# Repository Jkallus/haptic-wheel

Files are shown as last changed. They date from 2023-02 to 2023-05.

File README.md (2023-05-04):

# Haptic Volume Knob
Haptic feedback wheel implementing a volume knob. Inspired by Scott Bezek's Smart Knob and University of Michigan EECS 461 Haptics Lab

This volume knob is implemented with a feedback controlled motor and software rather than mechanical notches. When you turn it with your hand you feel real feedback force just as if it were an actual precisely made mechanical knob. Haptic Volume Knob works by monitoring the motor shaft's angle and applying the appropriate torque to implement the knob's feeling for that position. An ESP32 S3 monitors this position and commands a torque 7,000 times per second to give real time feedback that is convincing to a user as well as implements a stable control loop.

Two haptic effects are implemented here: A virtual knob with detents and a virtual wall which creates the sensation of the knob reaching end of travel. These sensations can be customized to feel "harder" or "softer" depending on spring constants. There is a button on the back of the enclosure to iterate through different knob detent feelings ranging from very light to very stiff. This variable haptic effect cannot be acheived with a traditional knob. 

The ESP32 communicates with the PC using HID. The TinyUSB HID library allows the ESP32 to describe itself as a custom HID device. It sends volume updates to Windows in the same way as the volume up and down keys on any keyboard work. The ESP32 gets the initial volume and any updates to the volume level made elsewhere by a service running on Windows which monitors volume changes and sends updates as HID reports. 

# Bill of Materials
| Item | Source | | | |
|---|---|---|---|---|
| ESP32 S3 | https://www.amazon.com/Teyleten-Robot-ESP32-S3-DevKitC-1-N8R2-Development-Integrates/dp/B0B6HT7V7P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 | | | |
| Busboard ST2 | https://www.amazon.com/Busboard-ST2-Traditional-Stripboard-Prototyping/dp/B00LLQFRAU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 | | | |
| TMC6300 Brushless Motor Driver  | https://www.sparkfun.com/products/retired/21220 | | | |
| Three Phase Brushless Motor | https://www.sparkfun.com/products/20441 | | | |
| AS5048A Magnetic Rotary Encoder | https://www.digikey.com/en/products/detail/ams-osram/AS5048A-TS-EK-AB/3188612 | | | |
| Neopixel 24 LED Ring | https://www.adafruit.com/product/1586 | | | |
| BH1750 Light Sensor | https://www.amazon.com/ACEIRMC-BH1750FVI-Intensity-Illumination-arduino/dp/B08ZS4PJSW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 | | | |
| LM2596 Buck Converter | https://www.amazon.com/Converter-Adjustable-Regulator-Efficiency-Transformer/dp/B08L5VRBZS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 | | | |
| Panel Mount Button | https://www.amazon.com/dp/B0752RMB7Q?psc=1&ref=ppx_yo2ov_dt_b_product_details | | | |
| DC Socket | https://www.amazon.com/dp/B082GHXS1Q?psc=1&ref=ppx_yo2ov_dt_b_product_details | | | |
| Micro USB Female Breakout | https://www.amazon.com/gp/product/B07T91S7L2/ref=ppx_yo_dt_b_search_asin_title?ie=UTF8&psc=1 | | | |
| PH 2.0 Crimp | https://www.amazon.com/gp/product/B07VHCFGZS/ref=ppx_yo_dt_b_search_asin_title?ie=UTF8&psc=1 | | | |
| | | | | |
| | | | | |

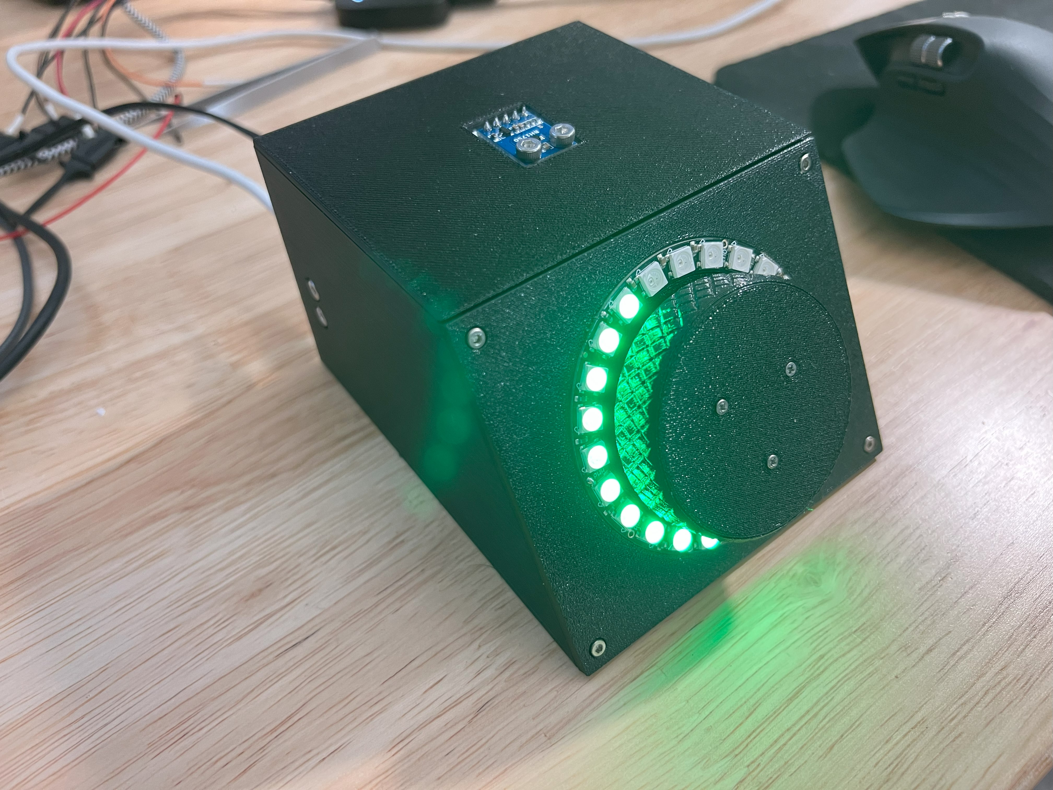
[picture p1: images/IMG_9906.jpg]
View 1

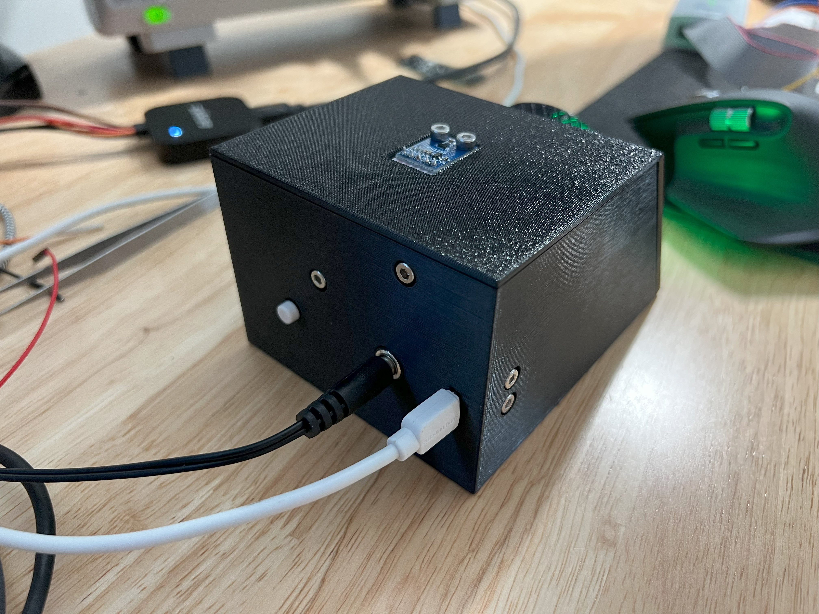
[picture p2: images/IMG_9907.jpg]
View 2

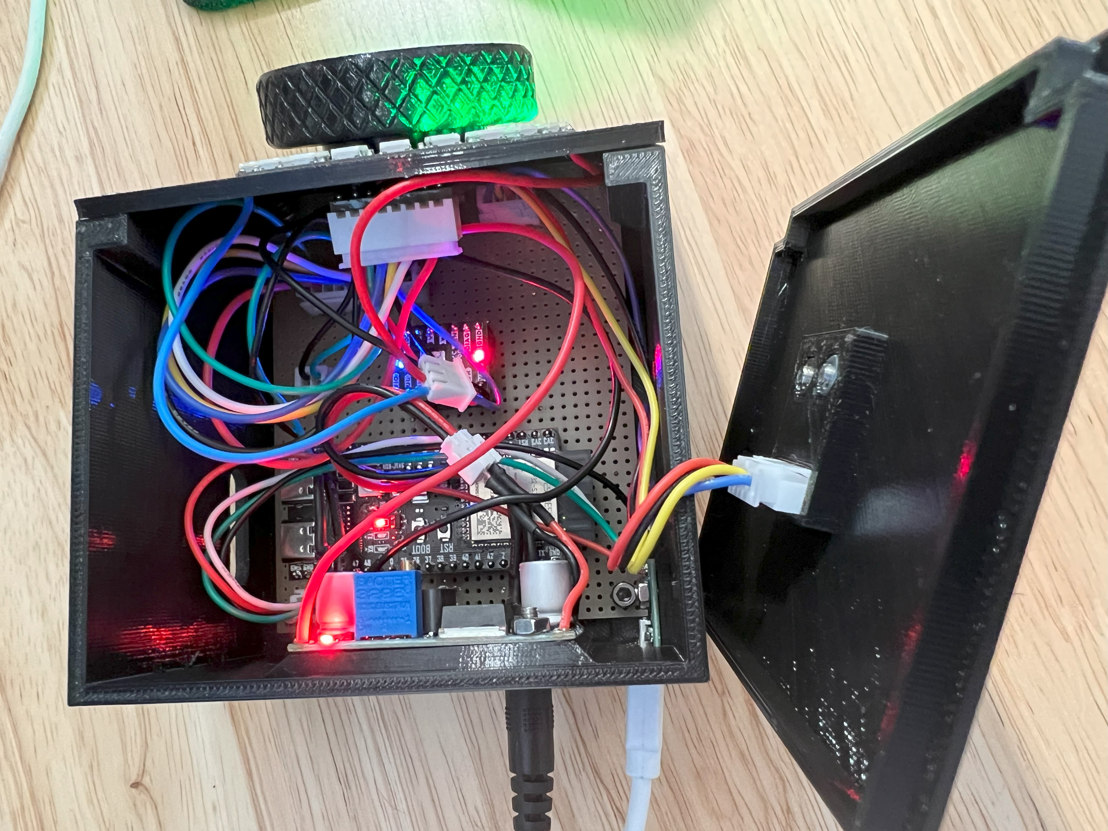
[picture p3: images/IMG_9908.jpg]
View 3


# Install Service
In powershell run the following line replacing paths with your own
`New-Service -Name "HIDVolumeSync" -BinaryPathName "C:\Users\joshk\source\repos\haptic-wheel\HID Volume Sync Service\bin\Debug\HID Volume Sync Service.exe"`
 
Make sure the service is set to startup type automatic in the Windows Services UI to start on boot up.

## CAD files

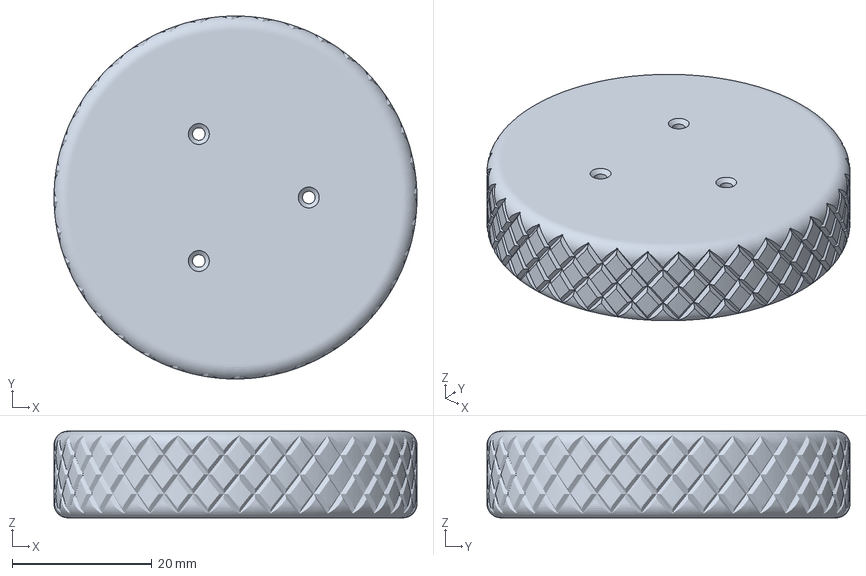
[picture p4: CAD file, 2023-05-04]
cad/Final Knob.3MF
52.0 x 52.0 x 12.4 mm

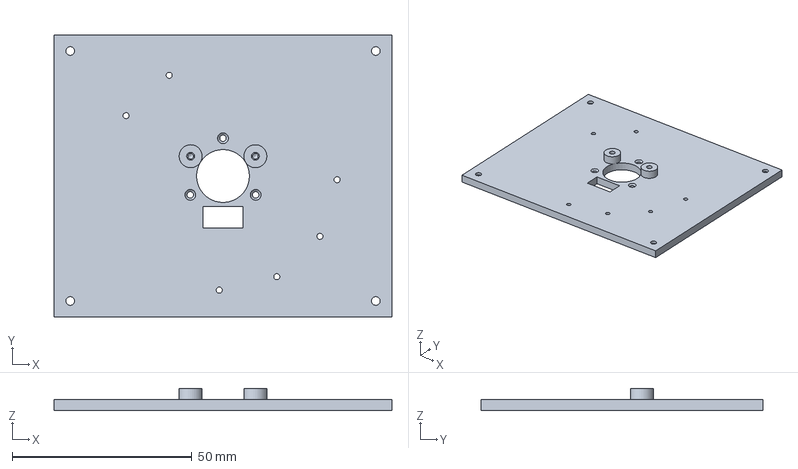
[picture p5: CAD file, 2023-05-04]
cad/Wheel Face.3MF
94.0 x 78.5 x 6.12 mm

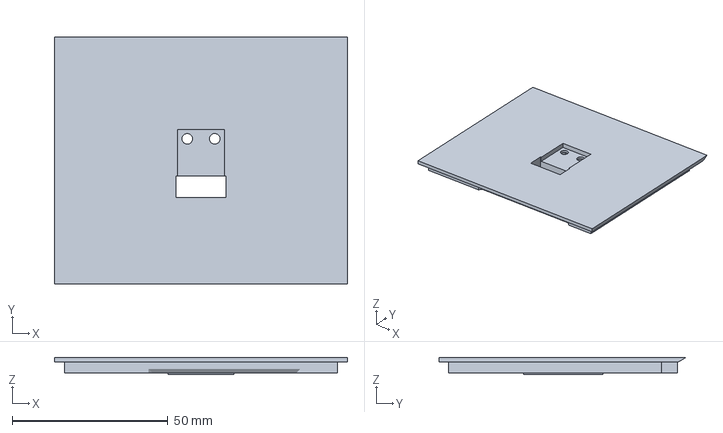
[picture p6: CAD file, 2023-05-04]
cad/Lid.3MF
94.0 x 79.3 x 5.50 mm

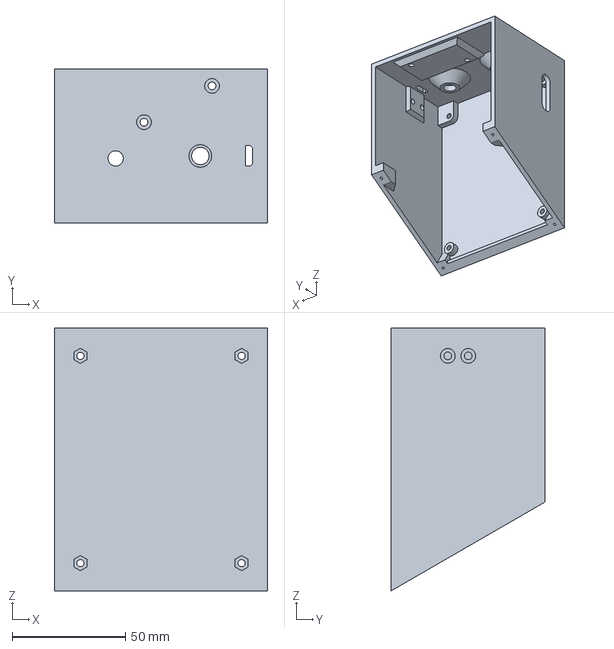
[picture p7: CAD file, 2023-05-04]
cad/Enclosure.3MF
94.0 x 68.0 x 116.0 mm

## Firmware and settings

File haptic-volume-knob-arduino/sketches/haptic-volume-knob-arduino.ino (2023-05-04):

/*
 *  Haptic Volume Knob
 *	MIT License
 *	
 *	Copyright 2023 Josh Kallus
 *	
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
 *	TODO: Check initial setting and make sure its not detecting a change there
 *	TODO: Motor rapidly moves sometimes when volume set externally reaches 100% or 0%
 *	TODO: End of travel angle can move further in a direction when repeatedly going to EOT and backing off. Not a huge deal but should be figured out
 */

#include "USB.h"
#include "USBHID.h"
#include <SimpleFOC.h>
#include <Adafruit_NeoPixel.h>
#include <Wire.h>
#include <BH1750.h>

#ifdef LOG_LOCAL_LEVEL
	#undef LOG_LOCAL_LEVEL
#endif

#define LOG_LOCAL_LEVEL ESP_LOG_WARN

////////////////// HID Config ////////////////////
const char* HID_TAG = "HID";
const char* MOTOR_TAG = "MOTOR";
const char* VOLUME_TAG = "VOLUME";
const char* MAIN_TAG = "MAIN";
const char* LED_TAG = "LED";
const char* BUTTON_TAG = "BUTTON";
static const uint8_t report_descriptor[] = { // 8 axis
    0x05, 0x0C,    // UsagePage(Consumer[12])
    0x09, 0x01,    // UsageId(Consumer Control[1])
    0xA1, 0x01,    // Collection(Application)
    0x85, 0x01,    //     ReportId(1)
    0x09, 0xE9,    //     UsageId(Volume Increment[233])
    0x15, 0x00,    //     LogicalMinimum(0)
    0x25, 0x01,    //     LogicalMaximum(1)
    0x95, 0x01,    //     ReportCount(1)
    0x75, 0x01,    //     ReportSize(1)
    0x81, 0x02,    //     Input(Data, Variable, Absolute, NoWrap, Linear, PreferredState, NoNullPosition, BitField)
    0x09, 0xEA,    //     UsageId(Volume Decrement[234])
    0x81, 0x02,    //     Input(Data, Variable, Absolute, NoWrap, Linear, PreferredState, NoNullPosition, BitField)
    0x75, 0x06,    //     ReportSize(6)
    0x81, 0x03,    //     Input(Constant, Variable, Absolute, NoWrap, Linear, PreferredState, NoNullPosition, BitField)
    0x09, 0xE0,    //     UsageId(Volume[224])
    0x15, 0xFF,    //     LogicalMinimum(-1)
    0x75, 0x02,    //     ReportSize(2)
    0x91, 0x02,    //     Output(Data, Variable, Absolute, NoWrap, Linear, PreferredState, NoNullPosition, NonVolatile, BitField)
    0x75, 0x06,    //     ReportSize(6)
    0x91, 0x03,    //     Output(Constant, Variable, Absolute, NoWrap, Linear, PreferredState, NoNullPosition, NonVolatile, BitField)
    0xC0,          // EndCollection()
};
USBHID HID;

////////////////// Motor Config //////////////////
#define A_h 18
#define A_l 8
#define B_h 16
#define B_l 17
#define C_h 7
#define C_l 15

enum class DETENTS_PER_REV
{
	Fifty      = 50,
	TwentyFive = 25,
};

constexpr DETENTS_PER_REV detents_per_revolution = DETENTS_PER_REV::Fifty;
constexpr float detent_width = 360.0f / (float)detents_per_revolution;
float detent_max_ma = 500;
float detent_max_ma_values[] = { 200, 300, 400, 500, 600, 700 };
constexpr float virtual_wall_ma_per_degree = 350;
float ma_per_degree = detent_max_ma / detent_width;

BLDCMotor motor = BLDCMotor(7);
BLDCDriver6PWM driver = BLDCDriver6PWM(A_h, A_l, B_h, B_l, C_h, C_l);
MagneticSensorSPI sensor = MagneticSensorSPI(AS5048_SPI, 10);

float init_angle = 0.0;
float max_angle = 0.0;
float last_current = 0.0;
float last_angle = 0.0;
float max_angle_threshold = 0.0; // angle threshold for CW after count = 50 (likely negative number)
float min_angle_threshold = 0.0; // angle threshold for CCW after count = 0 (likely positive number)
int count = 0; // number of detents were at out of max, 0...50 or 0...25. 
int i = 0; // loop variable
Commander command = Commander(Serial); // instantiate the commander
QueueHandle_t count_queue_handle = NULL;
TaskHandle_t count_change_internal_handle = NULL;

/////////////////////// Button Config //////////////////////////
gpio_num_t button_pin = GPIO_NUM_14;
QueueHandle_t button_message_queue = NULL;
TaskHandle_t button_task_handle = NULL;
unsigned long button_time = 0;
unsigned long last_button_time = 0;
uint32_t button_presses = 0;
void IRAM_ATTR button_isr()
{
	button_time = millis();
	BaseType_t xHigherPriorityTaskWoken = pdFALSE;
	
	if (button_time - last_button_time > 350)
	{
		button_presses++;
		last_button_time = button_time;
		xQueueSendFromISR(button_message_queue, &button_presses, &xHigherPriorityTaskWoken);
		
		if (xHigherPriorityTaskWoken)
		{
			portYIELD_FROM_ISR();
		}
	}
}

//////////////// LED Config ////////////////////////
#define LED_PIN 9
#define LED_COUNT 24
Adafruit_NeoPixel strip(LED_COUNT, LED_PIN, NEO_GRB + NEO_KHZ800);
QueueHandle_t led_state_queue_handle = NULL;
TaskHandle_t led_task_handle = NULL;
int led_order[24] = {7, 8, 9, 10, 11, 12, 13, 14, 15, 16, 17, 18, 19, 20, 21, 22, 23, 0, 1, 2, 3, 4, 5, 6};

//////////////// Light Sensor Config ///////////////////

#define SDA_PIN 38
#define SCL_PIN 37
TaskHandle_t light_monitor_task_handle;
BH1750 lightMeter;

void setup_light_sensor()
{
	ESP_LOGI(LED_TAG, "Setting up light sensor");
	Wire.setPins(SDA_PIN, SCL_PIN);
	Wire.begin();
	if (!lightMeter.begin())
	{
		ESP_LOGE(LED_TAG, "Light sensor failed to start");
	}
}

float get_light_level()
{
	return lightMeter.readLightLevel();
}

int calculate_brightness_for_lux(float lux)
{
	if (lux < 5) // Just computer monitor brightness
	{
		return 10;
	}
	else if (lux < 30) // Just one lamp far away
	{
		return 15;
	}
	else if (lux < 500) // Just one lamp close by
	{
		return 30;
	}
	else if(lux < 3000)
	{
		return 50;
	}
	else if(lux < 10000)
	{
		return 80;
	}
	else
	{
		return 255;
	}
}

int get_best_led_level()
{
	float val = get_light_level();
	int setting = calculate_brightness_for_lux(val);
	ESP_LOGI(LED_TAG, "Measured %f lux, setting LED brightness to %d", val, setting);
	return setting;
}

void light_monitor_task(void* arg)
{
	while (1)
	{
		strip.setBrightness(get_best_led_level());
		vTaskDelay(pdMS_TO_TICKS(1000)); // update brightness every 5 seconds
	}
}

uint8_t ConvertVolumeLevelToCount(uint8_t volume_level) // returns the count associated with a volume level
{
	if (detents_per_revolution == DETENTS_PER_REV::Fifty)
	{
		return volume_level / 2;
	}
	else
	{
		return volume_level / 4;
	}
}
	
uint8_t  ConvertCountToVolumeLevel(uint8_t count)
{
	if (detents_per_revolution == DETENTS_PER_REV::Fifty)
	{
		return count * 2;
	}
	else
	{
		return count * 4;
	}
}

class CustomHIDDevice : public USBHIDDevice {
public:
	CustomHIDDevice(void) {
		static bool initialized = false;
		if (!initialized) {
			initialized = true;
			HID.addDevice(this, sizeof(report_descriptor));
		}
	}
  
	void begin(void) {
		HID.begin();
	}

	void _onOutput(uint8_t report_id, const uint8_t* buffer, uint16_t len) override
	{
		if (!_received_first_volume) // This is the initial volume setting
		{
			_volume_level = buffer[0];
			ESP_LOGI(HID_TAG, "Received first volume data: %d", _volume_level);
			_received_first_volume = true;
			return;
		}
		else // Volume has changed outside of this device or we're getting confirmation of a recent change origination here
		{
			uint8_t new_volume_level = buffer[0];
			//ESP_LOGI(HID_TAG, "Got feedback, _device_volume is %d and new volume received is %d", _volume_level, new_volume_level);
			
			if (new_volume_level == _volume_level) // This is just a message confirming our recent change
			{
				//ESP_LOGI(HID_TAG, "Received data is confirming recent change made by this device");
			}
			else // Volume has adjusted from outside
			{
				//ESP_LOGI(HID_TAG, "Received data is different value and change needs to be accounted for");
				SetVolumeLevelExternal(new_volume_level);
			}
		}
	}
	
	uint8_t GetVolumeLevel()
	{
		return _volume_level;
	}
	
	// Set the volume level from a change that occured outside the system
	void SetVolumeLevelExternal(uint8_t volume)
	{
		send_led_message_volume_level(volume); // Need to set LEDs
		uint8_t new_count = ConvertVolumeLevelToCount(volume);
		count = new_count; // Need to change count to reflect new status
		if (volume == 100) // If external changes have moved it to 100 or 0 percent then the angle limit needs to be set again
		{
			max_angle_threshold = sensor.getSensorAngle() * (180 / PI) - detent_width / 2;
			ESP_LOGI(MOTOR_TAG, "Volume changed from outside and is now at 100, setting CW threshold angle to %f", max_angle_threshold);
		}
		else if (volume == 0)
		{
			min_angle_threshold = sensor.getSensorAngle() * (180 / PI) + detent_width / 2;
			ESP_LOGI(MOTOR_TAG, "Volume changed from outside and is now at 0, setting CCW threshold angle to %f", min_angle_threshold);
		}
		_volume_level = volume;
	}
	
	// Set the volume level from a change that occured inside the system
	void SetVolumeLevelInternal(uint8_t volume) // Assumed to be 0...100 in increments of 2
	{
		// Need to send update over HID
		if (volume > _volume_level) // volume increment
		{
			uint8_t increment_counts = (volume - _volume_level) % 2;
			increment(increment_counts);
		}
		else // volume decrement
		{
			uint8_t decrement_counts = (_volume_level - volume) % 2;
			decrement(decrement_counts);
		}
		send_led_message_volume_level(volume); // Need to set LEDs
		_volume_level = volume;
	}
	
	void block_till_first_volume()
	{
		while (!_received_first_volume)
		{
			vTaskDelay(pdMS_TO_TICKS(10));
		}
	}

	uint16_t _onGetDescriptor(uint8_t* buffer) {
		memcpy(buffer, report_descriptor, sizeof(report_descriptor));
		return sizeof(report_descriptor);
	}

	bool increment(int counts = 1)
	{
		for (int k = 0; k < counts; k++)
		{
			uint8_t data[1];
			data[0] = 0x01;
			HID.SendReport(1, data, 1);
			data[0] = 0x00;
			return HID.SendReport(1, data, 1);	
			ESP_LOGI(VOLUME_TAG, "Incrementing volume");
		}
	}
	
	bool decrement(int counts = 1)
	{
		for (int k = 0; k < counts; k++)
		{
			uint8_t data[1];
			data[0] = 0x02;
			HID.SendReport(1, data, 1);
			data[0] = 0x00;
			return HID.SendReport(1, data, 1);
			ESP_LOGI(VOLUME_TAG, "Decrementing volume");
		}
	}

	bool send(uint8_t * value) {
		return HID.SendReport(0, value, 8);
	}
	
private:
	uint8_t _volume_level = 0;
	bool _received_first_volume = false;
};
CustomHIDDevice Device;

void count_change_internal_task(void* arg) // Receives new count value from queue
{
	int new_count;
	while (1)
	{
		if (xQueueReceive(count_queue_handle, &new_count, (TickType_t)5))
		{
			Device.SetVolumeLevelInternal(ConvertCountToVolumeLevel((uint8_t)new_count)); // how to handle negative count values? Should never occur in practice
		}
	}
}

void button_handler_task(void* arg)
{
	uint32_t value;
	while (1)
	{
		if (xQueueReceive(button_message_queue, &value, (TickType_t)5))
		{
			int idx = value % (sizeof(detent_max_ma_values) / sizeof(detent_max_ma_values[0]));
			detent_max_ma = detent_max_ma_values[idx];
			ma_per_degree = detent_max_ma / detent_width;
			ESP_LOGI(BUTTON_TAG, "Got button press %d, setting current to idx %d, value %f", value, index, detent_max_ma);
		}
		vTaskDelay(pdMS_TO_TICKS(250));
	}
}

void setup_motor()
{
	sensor.init(); // initialise magnetic sensor hardware
	motor.linkSensor(&sensor); // link the motor to the sensor

	// driver config
	driver.voltage_power_supply = 10; // power supply voltage [V]
	driver.init();
	
	// motor config
	motor.linkDriver(&driver); // link driver
	motor.phase_resistance = 5; // this sets align voltage too
	motor.current_limit = 1.0;
	motor.torque_controller = TorqueControlType::voltage;
	motor.controller = MotionControlType::torque; // set motion control loop to be used
	
	Serial.begin(115200); // use monitoring with serial 
	
	motor.init();
	motor.initFOC(); // align sensor and start FOC

	ESP_LOGI(MOTOR_TAG, "Motor ready");
	vTaskDelay(pdMS_TO_TICKS(1000));
	init_angle = sensor.getSensorAngle() * (180 / PI);
	ESP_LOGI(MOTOR_TAG, "Init angle: %d, Max angle: %d", init_angle, max_angle);
}

//////////////////// LED Functions ///////////////////////////////////
void send_led_message_count(uint8_t count)
{
	xQueueSend(led_state_queue_handle, &count, (TickType_t)5);
}

void send_led_message_volume_level(uint8_t volume_level)
{
	send_led_message_count(ConvertVolumeLevelToCount(volume_level));
}
void led_control_task(void* arg) // Receives volume level in detent counts
{
	uint8_t count_received;
	while (1)
	{
		if(xQueueReceive(led_state_queue_handle, &count_received, (TickType_t)5))
		{
			float levels_per_led = (float)detents_per_revolution / (float)LED_COUNT;
			int fully_lit_count = (int)(count_received / levels_per_led);
			float remainder = fmod(count_received, levels_per_led);
			float last_led_percentage = remainder / levels_per_led;
			set_strip(fully_lit_count, last_led_percentage);
		}
		vTaskDelay(10);
	}
}

void set_strip(int fully_lit, float last_percent)
{
	strip.clear();
	for (int j = 0; j < fully_lit; j++)
	{
		strip.setPixelColor(led_order[j], 0, 255, 0);
	}
	if (last_percent > 0.001 && fully_lit < LED_COUNT) 
	{
		int brightness = (int)(last_percent * 255);
		int last_led_idx = led_order[fully_lit]; 
		strip.setPixelColor(last_led_idx, 0, brightness, 0);
	}
	strip.show();
}

void set_strip_single_color(uint8_t red, uint8_t green, uint8_t blue)
{
	for (int i = 0; i < LED_COUNT; i++)
	{
		strip.setPixelColor(i, red, green, blue);
	}
	strip.show();
}

void setup()
{
	Serial.begin(115200);
	ESP_LOGI(MAIN_TAG, "Started setup");
	
	// Setup light sensor to set led strip
	setup_light_sensor();
	
	// Set strip up first to show init sequence
	strip.begin();
	strip.show();
	strip.clear();
	strip.setBrightness(get_best_led_level());
	set_strip_single_color(50, 0, 0);
	
	// Setup USB to begin waiting for first volume
	Device.begin();
	USB.begin();
	
	// This takes a while
	setup_motor();
	pinMode(4, OUTPUT);
	
	// Wait to get volume
	Device.block_till_first_volume();
	uint8_t initial_volume = Device.GetVolumeLevel();
	
	// Count starts at 0 and has range of 0...detents/revolution
	float volume_as_percent = (float)initial_volume / 100.0f;
	int initial_count = (int) (volume_as_percent * (float) detents_per_revolution);
	ESP_LOGI("MOTOR", "Setting inital count to %d", initial_count);
	count = initial_count;
	
	count_queue_handle = xQueueCreate(5, sizeof(int));
	led_state_queue_handle = xQueueCreate(5, sizeof(uint8_t));
	
	pinMode(button_pin, INPUT_PULLUP);
	button_message_queue = xQueueCreate(5, sizeof(uint32_t));
	attachInterrupt(button_pin, button_isr, FALLING);
	
	xTaskCreate(count_change_internal_task, "Count Change Internal Task", 2048, NULL, configMAX_PRIORITIES - 5, &count_change_internal_handle);
	xTaskCreate(led_control_task, "LED control task", 2048, NULL, configMAX_PRIORITIES - 6, &led_task_handle);
	xTaskCreate(light_monitor_task, "Light monitor task", 4096, NULL, configMAX_PRIORITIES - 10, &light_monitor_task_handle);
	xTaskCreate(button_handler_task, "Button monitor task", 2048, NULL, configMAX_PRIORITIES - 9, &button_task_handle);
	
	xQueueSend(count_queue_handle, &count, (TickType_t)5);
}

void loop()
{
	digitalWrite(4, HIGH);
	motor.loopFOC();
	
	float angle_rad = sensor.getAngle();
	float angle = angle_rad * (180 / PI);
	float spring_current = 0;
	float total_current = 0;
	
	float threshold = detent_width / 2;
	float angle_noise_threshold = 0.3;
	
	if (count >= ConvertVolumeLevelToCount(100) && angle < max_angle_threshold)
	{
		float degrees_past_edge = abs(angle - max_angle_threshold);
		spring_current = (virtual_wall_ma_per_degree / 1000.0) * degrees_past_edge * -1;
		motor.move(spring_current);
		return;
	}
	else if (count <= 0 && angle > min_angle_threshold)
	{
		float degrees_past_edge = abs(angle - min_angle_threshold);
		spring_current = (virtual_wall_ma_per_degree / 1000.0) * degrees_past_edge;
		motor.move(spring_current);
		return;
	}
	
	if (angle > 0)
	{
		float phase = fmod(angle, detent_width);
		if (phase < threshold)
		{		
			if (last_current < 0)
			{
				if (abs(phase - threshold) > angle_noise_threshold)
				{
					spring_current = phase * (ma_per_degree / 1000.0);
				}
				else
				{
					spring_current = last_current;
				}
			}
			else
			{
				spring_current = phase * (ma_per_degree / 1000.0);
			}
		}
		else
		{
			if (last_current > 0)
			{
				if ((abs(phase - threshold)) > angle_noise_threshold)
				{
					float phase2 = fmod(phase, threshold);
					spring_current = (threshold - phase2) * (ma_per_degree / 1000.0) * -1;
				}
				else
				{
					spring_current = last_current;
				}
			}
			else
			{
				float phase2 = fmod(phase, threshold);
				spring_current = (threshold - phase2) * (ma_per_degree / 1000.0) * -1;
			}
		}
	}
	else
	{
		float phase = fmod(angle, detent_width);
		if (phase > -threshold)
		{
			if (last_current > 0)
			{
				if (abs(phase - -threshold) > angle_noise_threshold)
				{
					spring_current = phase * (ma_per_degree / 1000.0);
				}
				else
				{
					spring_current = last_current;
				}
			}
			else
			{
				spring_current = phase * (ma_per_degree / 1000.0);
			}
		}
		else
		{
			if (last_current < 0)
			{
				if ((abs(phase - -threshold)) > angle_noise_threshold)
				{
					float phase2 = fmod(phase, threshold);
					spring_current = (threshold + phase2) * (ma_per_degree / 1000.0);
				}
				else
				{
					spring_current = last_current;
				}
			}
			else
			{
				float phase2 = fmod(phase, threshold);
				spring_current = (threshold + phase2) * (ma_per_degree / 1000.0);
			}
		}
	}

	total_current = spring_current;
	if (total_current > 1.0)
		total_current = 1.0;
	else if (total_current < -1.0)
		total_current = -1.0;
	
	float peak_current_threshold = (ma_per_degree / 1000.0) * (detent_width / 2) * 0.9;
	bool at_snap_edge = abs(last_current) > peak_current_threshold && abs(total_current) > peak_current_threshold; // check that the transition that may be occuring is at the snap edge and not in the settling point between snaps
	if (last_current > 0 && total_current < 0 && at_snap_edge) // CCW snap
	{
		count--;
		if (count == 0)
		{	
			min_angle_threshold = angle + (detent_width/2);
			ESP_LOGI(MOTOR_TAG, "Reached min count: %d at angle: %f, setting CCW threshold to %f", count, angle, min_angle_threshold);
		}
		ESP_LOGI(MOTOR_TAG, "Detected decrement, count value now: %d, angle: %f",count, angle);
		xQueueSend(count_queue_handle, &count, (TickType_t)5);
	}
	else if(last_current < 0 && total_current > 0 && at_snap_edge) // CW snap
	{
		count++;
		if (count == ConvertVolumeLevelToCount(100))
		{
			max_angle_threshold = angle - (detent_width/2); // at snap angle, it settles detent_width/2 further
			ESP_LOGI(MOTOR_TAG, "Reached max count: %d at angle: %f, setting CW threshold to %f", count, angle, max_angle_threshold);
		}
		ESP_LOGI(MOTOR_TAG, "Detected increment, count value now: %d, angle: %f", count, angle);
		xQueueSend(count_queue_handle, &count, (TickType_t)5);
	}
	
	last_current = total_current;
	motor.move(total_current);
	digitalWrite(4, LOW);
}

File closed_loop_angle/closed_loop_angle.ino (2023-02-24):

#include <SimpleFOC.h>

#define A_h 17 
#define A_l 16
#define B_h 26
#define B_l 25
#define C_h 22
#define C_l 21

// BLDC motor & driver instance
BLDCMotor motor = BLDCMotor(7);
BLDCDriver6PWM driver = BLDCDriver6PWM(A_h, A_l, B_h, B_l, C_h, C_l);

// magnetic sensor instance - SPI
MagneticSensorSPI sensor = MagneticSensorSPI(AS5048_SPI, 5);

float target_angle = 1;

// instantiate the commander
Commander command = Commander(Serial);
void doTarget(char* cmd) { command.scalar(&target_angle, cmd); }
void doMotor(char* cmd) { command.motor(&motor, cmd); }
void setup() { 
  
  // initialise magnetic sensor hardware
  sensor.init();
  // link the motor to the sensor
  motor.linkSensor(&sensor);

  // driver config
  // power supply voltage [V]
  driver.voltage_power_supply = 10;
  driver.init();
  // link driver
  motor.linkDriver(&driver);

  // aligning voltage
  motor.phase_resistance = 5;
  motor.current_limit = 1.0;
  motor.velocity_limit = 10;
  // set motion control loop to be used
  motor.controller = MotionControlType::angle;
  //motor.torque_controller = TorqueControlType::voltage;
  
  // velocity PI controller parameters
  motor.PID_velocity.P = 0.07;
  motor.PID_velocity.I = 5.0;
  motor.PID_velocity.D = 0.0;
  motor.PID_velocity.output_ramp = 1000;
  motor.LPF_velocity.Tf = 0.01f;

 // angle P controller
  motor.P_angle.P = 20;

  // use monitoring with serial 
  Serial.begin(115200);
  // comment out if not needed
  motor.useMonitoring(Serial);
  motor.monitor_variables = _MON_TARGET | _MON_VEL | _MON_ANGLE;
  // initialize motor
  motor.init();
  // align sensor and start FOC
  motor.initFOC();

  // set the initial motor target
  //motor.target = 0.2; // Amps - if phase resistance defined  
  //motor.target = 2; // Volts 

  // add target command T
  command.add('T', doTarget, "target velocity");
  command.add('M', doMotor, "motor");
  //command.add('T', doTarget, "target voltage");

  Serial.println(F("Motor ready."));
  Serial.println(F("Set the target using serial terminal:"));
  _delay(1000);
}



void loop() {
  // main FOC algorithm function
  motor.loopFOC();

  // Motion control function
  motor.move(target_angle);

  //motor.monitor();

  // user communication
  command.run();
}

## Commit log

2023-03-10 Added captured data and C# and Matlab to process it
    [spi_capture.csv, spi_capture_small.csv]
2023-03-10 Changed algorithm for detents to not rapidly flip current due to angle noise. Angle noise is measured to be .07 degrees.
2023-04-01 Prototype working in arduino
2023-04-03 Added volume monitoring and updating HID device
2023-04-03 Finished initial version of main features. Virtual wall implemented and state synchronization between device and PC is working
2023-04-05 Added button control of torque and made led order changeable
2023-04-17 Cleaned up arduino code
2023-05-04 Change pins for PCB version, added back some logging for button
2023-05-04 Added files for 3D printed parts
    [Enclosure.3MF, Final Knob.3MF, Lid.3MF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]
2023-05-04 Add more description and links for BOM
